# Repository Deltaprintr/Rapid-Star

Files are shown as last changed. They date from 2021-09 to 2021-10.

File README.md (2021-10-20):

Rapid Star Image

# Overview

Rapid Star is a PNP (Pick and Place) system developed and maintained by [Deltaprintr](https://deltaprintr.com), run on the free [OpenPNP Software](https://openpnp.org) and [Mark's Smoothieware Firmware Version](https://makr.zone/smoothieware-new-firmware-for-pnp/500/) used for assembling circuit boards with the [Rapid Feeder](https://www.deltaprintr.com/product/rapid-feeder/) system. It features a conveyor belt that can hold boards up to 165mm (6.5") wide, 50 (8mm) feeders and has a head capable of supporting up to 8 nozzles with a 20 nozzle magazine auto-changer. Documentation on building a Rapid Star can be found [on our website](https://www.deltaprintr.com/docs/rapid-star/). The release is considered stable as the machine has been fully tested manually. If you would like to show your support for the project, consider purchasing [components directly from Deltaprintr](https://www.deltaprintr.com/product-category/smt-assembly/). This not only allows us to continue developing the Rapid Star, but also enables us to provide support directly to you in the process.

If you'd like to find out once Deltaprintr starts offering a complete kit, you can subscribe to our [mailing list](https://mailchi.mp/ee676e0cfc9f/rapidstar)

# Benefits of a star design
- Scalable nozzle count at no additional cost
- Higher CPH
- Simpler mechanical assembly
- More X/Y space due to smaller head, which means more space for feeders/trays.

# Contribute

Currently the Rapid Star is not fully supported in OpenPNP due to a few missing mandatory features. We're actively looking for developers who would be interested in helping us incorporate support into OpenPNP. You can see the [full list of features here](https://docs.google.com/document/d/1N6ggEopUlor0r7kC39QZDpr8pi3T8QCvNgg1l5aPtP0/edit?usp=sharing). If you're interested in helping, let us know on our [Discord Server](https://discord.gg/t2FcjAU7hC)!

If you'd like to keep up with the latest news you can also follow us on [Instagram](https://www.instagram.com/deltaprintr/), [Facebook](https://www.facebook.com/Deltaprintr/) or [Twitter](https://twitter.com/deltaprintr)!

# Support

While you are free to source and build a Rapid Star on your own, we are only able to provide support for customers who purchase components directly from us. This way we can guarantee your parts came from a reputable source and have a warranty. It's worth noting that some custom parts such as the head must be machined to a high tolerance to ensure air does not leak. For this reason, we recommend to get parts directly from us as it will save you time and frustration. However, if you do decide to source parts elsewhere, we do have a community of users who would be happy to help you on our [Discord Server](https://discord.gg/t2FcjAU7hC).

You can view a 3D model of the full assembly in your browser here: https://autode.sk/3zCK5wB

Support questions submitted via Github will be deleted. Only bugs/issues should be submitted via Github.

# Github Structure
- Mechanics (Full machine assembly)
- Electronics (Rapid Board, Conveyor, C Endstop, Nozzle Magazine, Feeder Extension, Feeder Motherboard)
- Firmware (Smoothieware and config)
- Openpnp Settings (OpenPNP machine.xml)
- Jigs (Lens calibration PCB)
- Scripts (Gcode for upward lens cam calibration)

# Programs Used
- Fusion 360
- Eagle CAD

# License

Rapid Star is licensed under [CC BY-NC-SA](https://creativecommons.org/licenses/by-nc-sa/4.0/): This license allows reusers to distribute, remix, adapt, and build upon the material in any medium or format for **non-commercial purposes only**, and only so long as attribution is given to the creator. If you remix, adapt, or build upon the material, you must license the modified material under identical terms. 

CC BY-NC-SA includes the following elements:

* BY  – Credit must be given to the creator
* NC  – Only non-commercial uses of the work are permitted
* SA  – Adaptations must be shared under the same terms

Deltaprintr, Rapid Star and Rapid Feeder are trademarks of Deltaprinter Inc. Other trademarks may be pending.

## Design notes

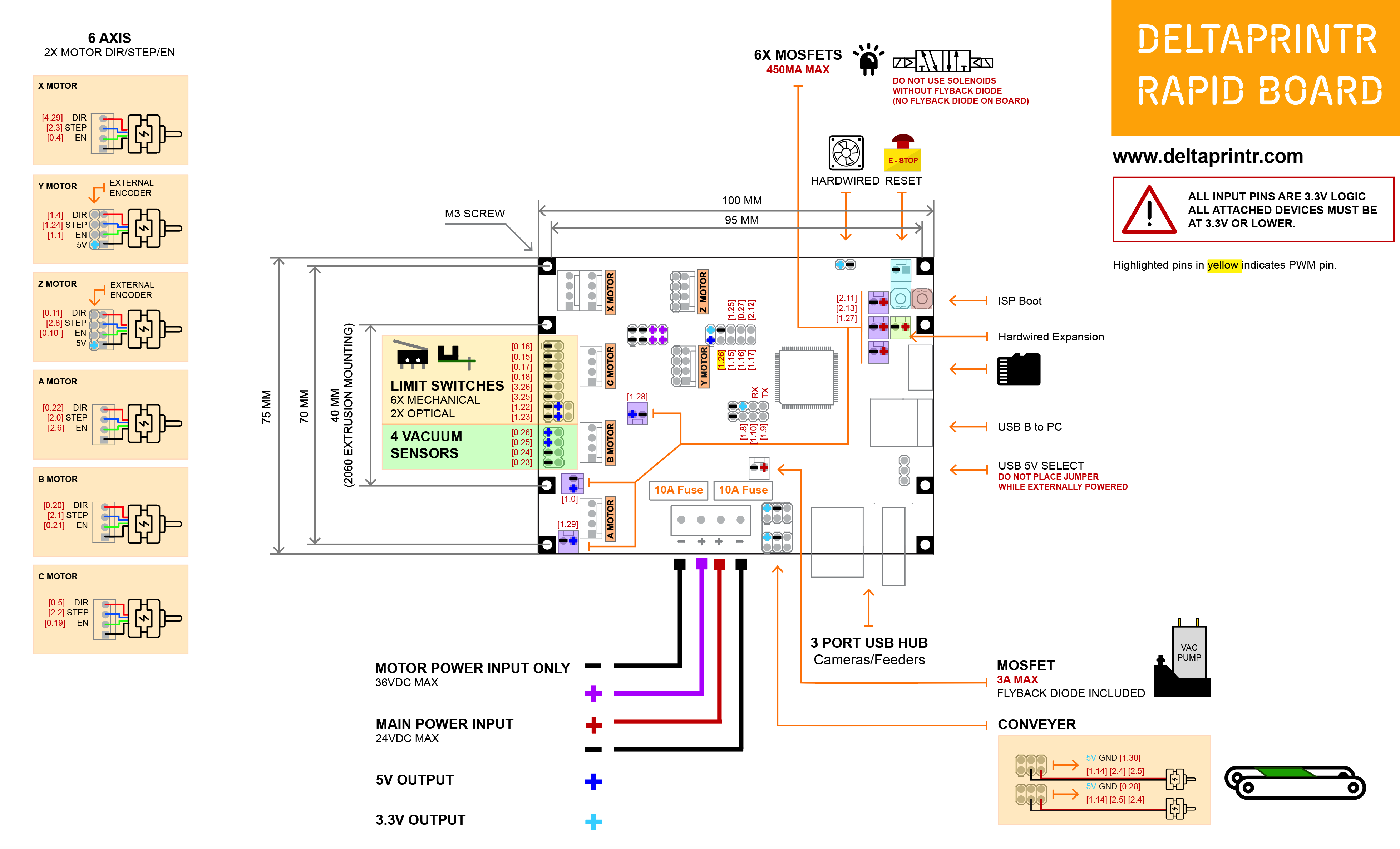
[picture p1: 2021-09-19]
Electronics/Rapid Board/Rapid Board Connections.png

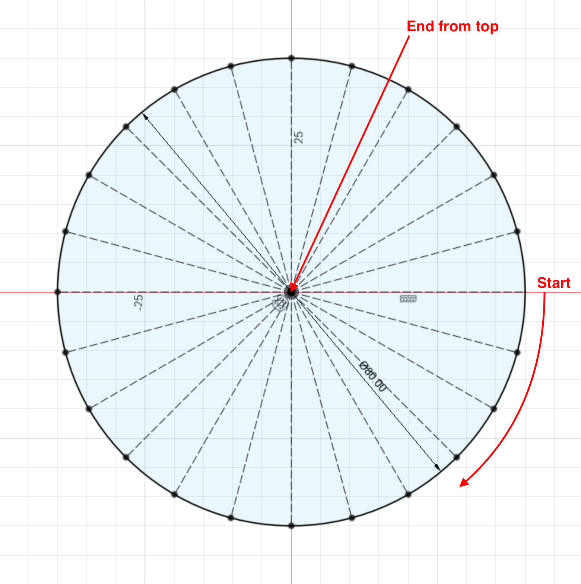
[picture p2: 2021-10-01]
Scripts/Upward Cam Gcode.png

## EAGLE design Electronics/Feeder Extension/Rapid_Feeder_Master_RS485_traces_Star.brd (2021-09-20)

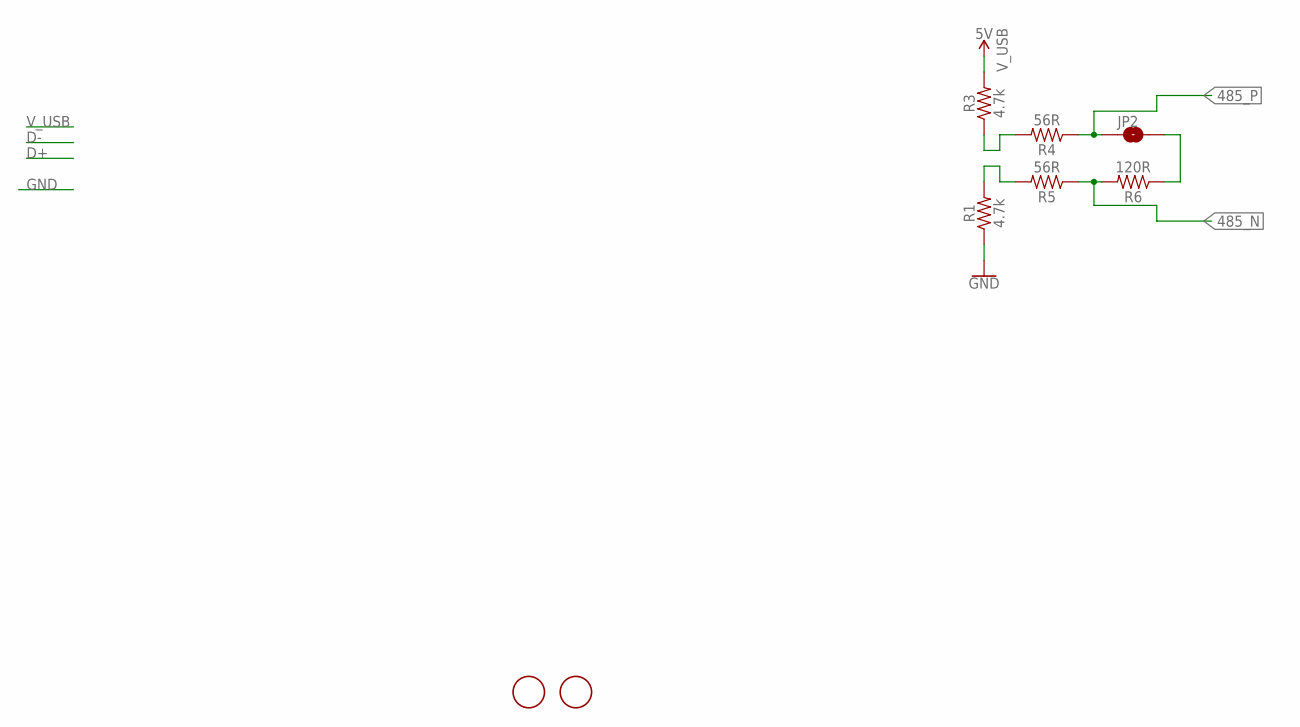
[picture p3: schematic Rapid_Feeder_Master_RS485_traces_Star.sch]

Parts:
JP2: JUMPER-SMT_2_NO_NO-SILK; SMT-JUMPER_2_NO_NO-SILK
R1, R3: 4.7k; R0603
R4, R5: 56R; R0603
R6: 120R; R0603
U$1, U$2: FIDUCIAL; FIDUCIAL_1MM

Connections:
485_N: R5.1, R6.2
485_P: JP2.1, R4.1
GND: R1.1
unnamed: R3.1, R4.2
unnamed: R1.2, R5.2
unnamed: JP2.2, R6.1
V_USB: R3.2

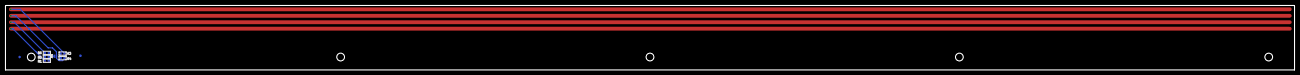
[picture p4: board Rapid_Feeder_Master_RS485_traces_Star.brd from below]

Board: 2 copper layers, 500.0 x 25.0 mm, 8 parts (8 on the bottom side), 5 nets.

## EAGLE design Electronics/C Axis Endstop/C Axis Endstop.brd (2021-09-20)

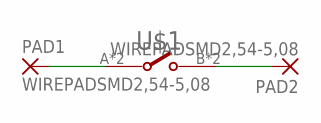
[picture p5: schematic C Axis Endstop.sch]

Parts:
PAD1, PAD2: WIREPADSMD2,54-5,08; SMD2,54-5,08
U$1: SWITCH_LIMIT_HDP001L

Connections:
unnamed: PAD1.1, U$1.A (1), U$1.C (1)
unnamed: PAD2.1, U$1.B (2), U$1.D (2)

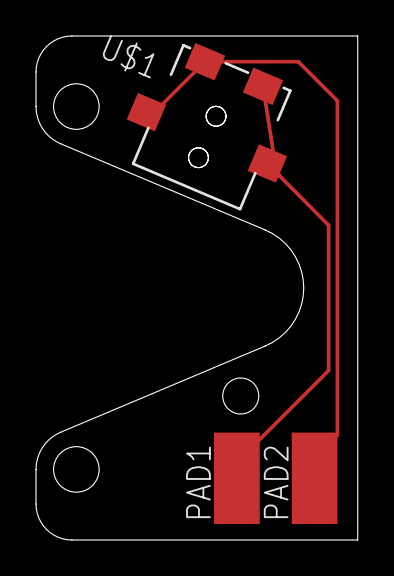
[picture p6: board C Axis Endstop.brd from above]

Board: 2 copper layers, 17.9 x 28.0 mm, 3 parts (0 on the bottom side), 2 nets.

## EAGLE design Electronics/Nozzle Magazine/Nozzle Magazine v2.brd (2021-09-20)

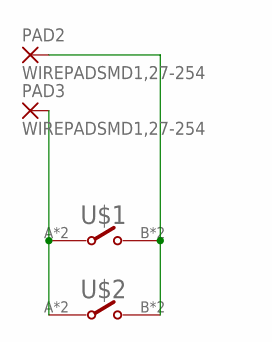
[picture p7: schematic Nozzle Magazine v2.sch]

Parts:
PAD2, PAD3: WIREPADSMD1,27-254; SMD1,27-2,54
U$1, U$2: SWITCH_LIMIT_HDP001L

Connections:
unnamed: PAD3.1, U$1.A (1), U$1.C (1), U$2.A (1), U$2.C (1)
unnamed: PAD2.1, U$1.B (2), U$1.D (2), U$2.B (2), U$2.D (2)

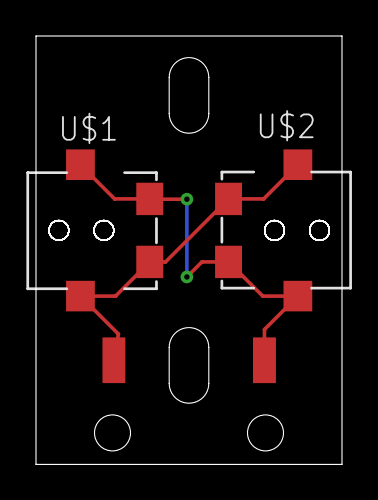
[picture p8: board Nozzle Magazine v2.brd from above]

Board: 2 copper layers, 17.0 x 23.8 mm, 4 parts (0 on the bottom side), 2 nets.

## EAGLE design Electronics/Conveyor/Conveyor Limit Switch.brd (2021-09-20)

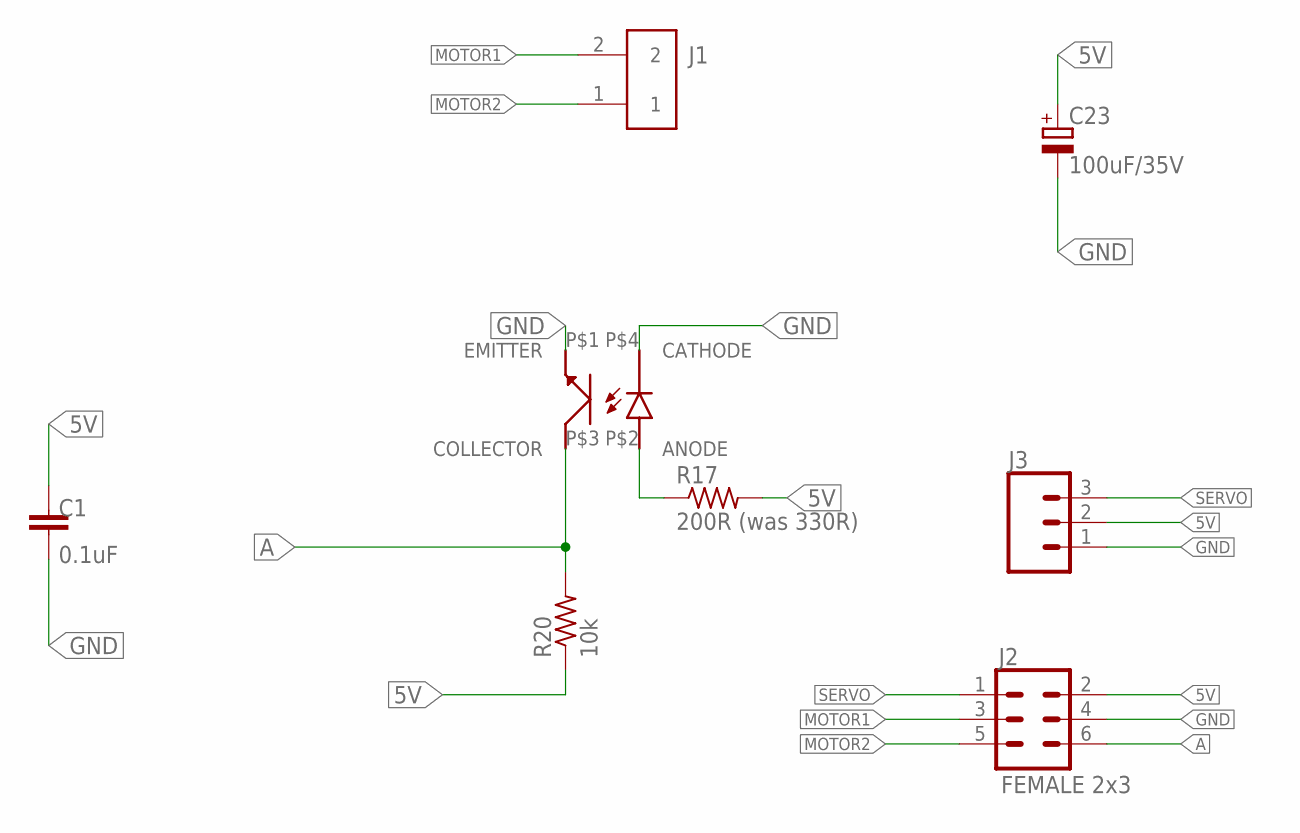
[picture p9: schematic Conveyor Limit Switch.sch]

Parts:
C1: 0.1uF; CAP_0603
C23: 100uF/35V; 153CLV-0605
J1: S2B-PH-SM4-TB(LF)(SN); S2B-PH-SM4-TB
J2: FEMALE 2x3; 2X3
J3: CONN_03; 1X03
R17: 200R (was 330R); RESISTOR_0603
R20: 10k; RESISTOR_0603
U$2: IR_VCNT2020

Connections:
5V: C1.1, C23.+, J2.2, J3.2, R17.2, R20.1
A: J2.6, R20.2, U$2.P$3 (COLLECTOR)
GND: C1.2, C23.-, J2.4, J3.1, U$2.P$1 (EMITTER), U$2.P$4 (CATHODE)
LED2: R17.1, U$2.P$2 (ANODE)
MOTOR1: J1.2, J2.3
MOTOR2: J1.1, J2.5
SERVO: J2.1, J3.3

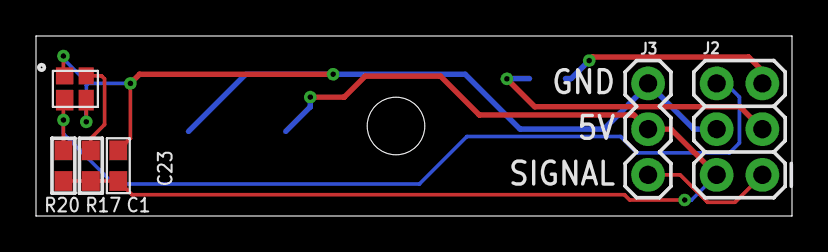
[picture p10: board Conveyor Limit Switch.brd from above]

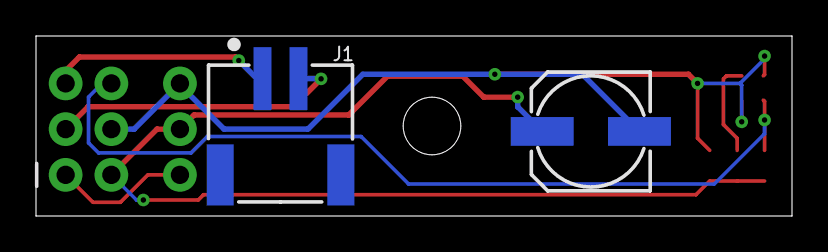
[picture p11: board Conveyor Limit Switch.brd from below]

Board: 2 copper layers, 42.0 x 10.0 mm, 8 parts (2 on the bottom side), 7 nets.

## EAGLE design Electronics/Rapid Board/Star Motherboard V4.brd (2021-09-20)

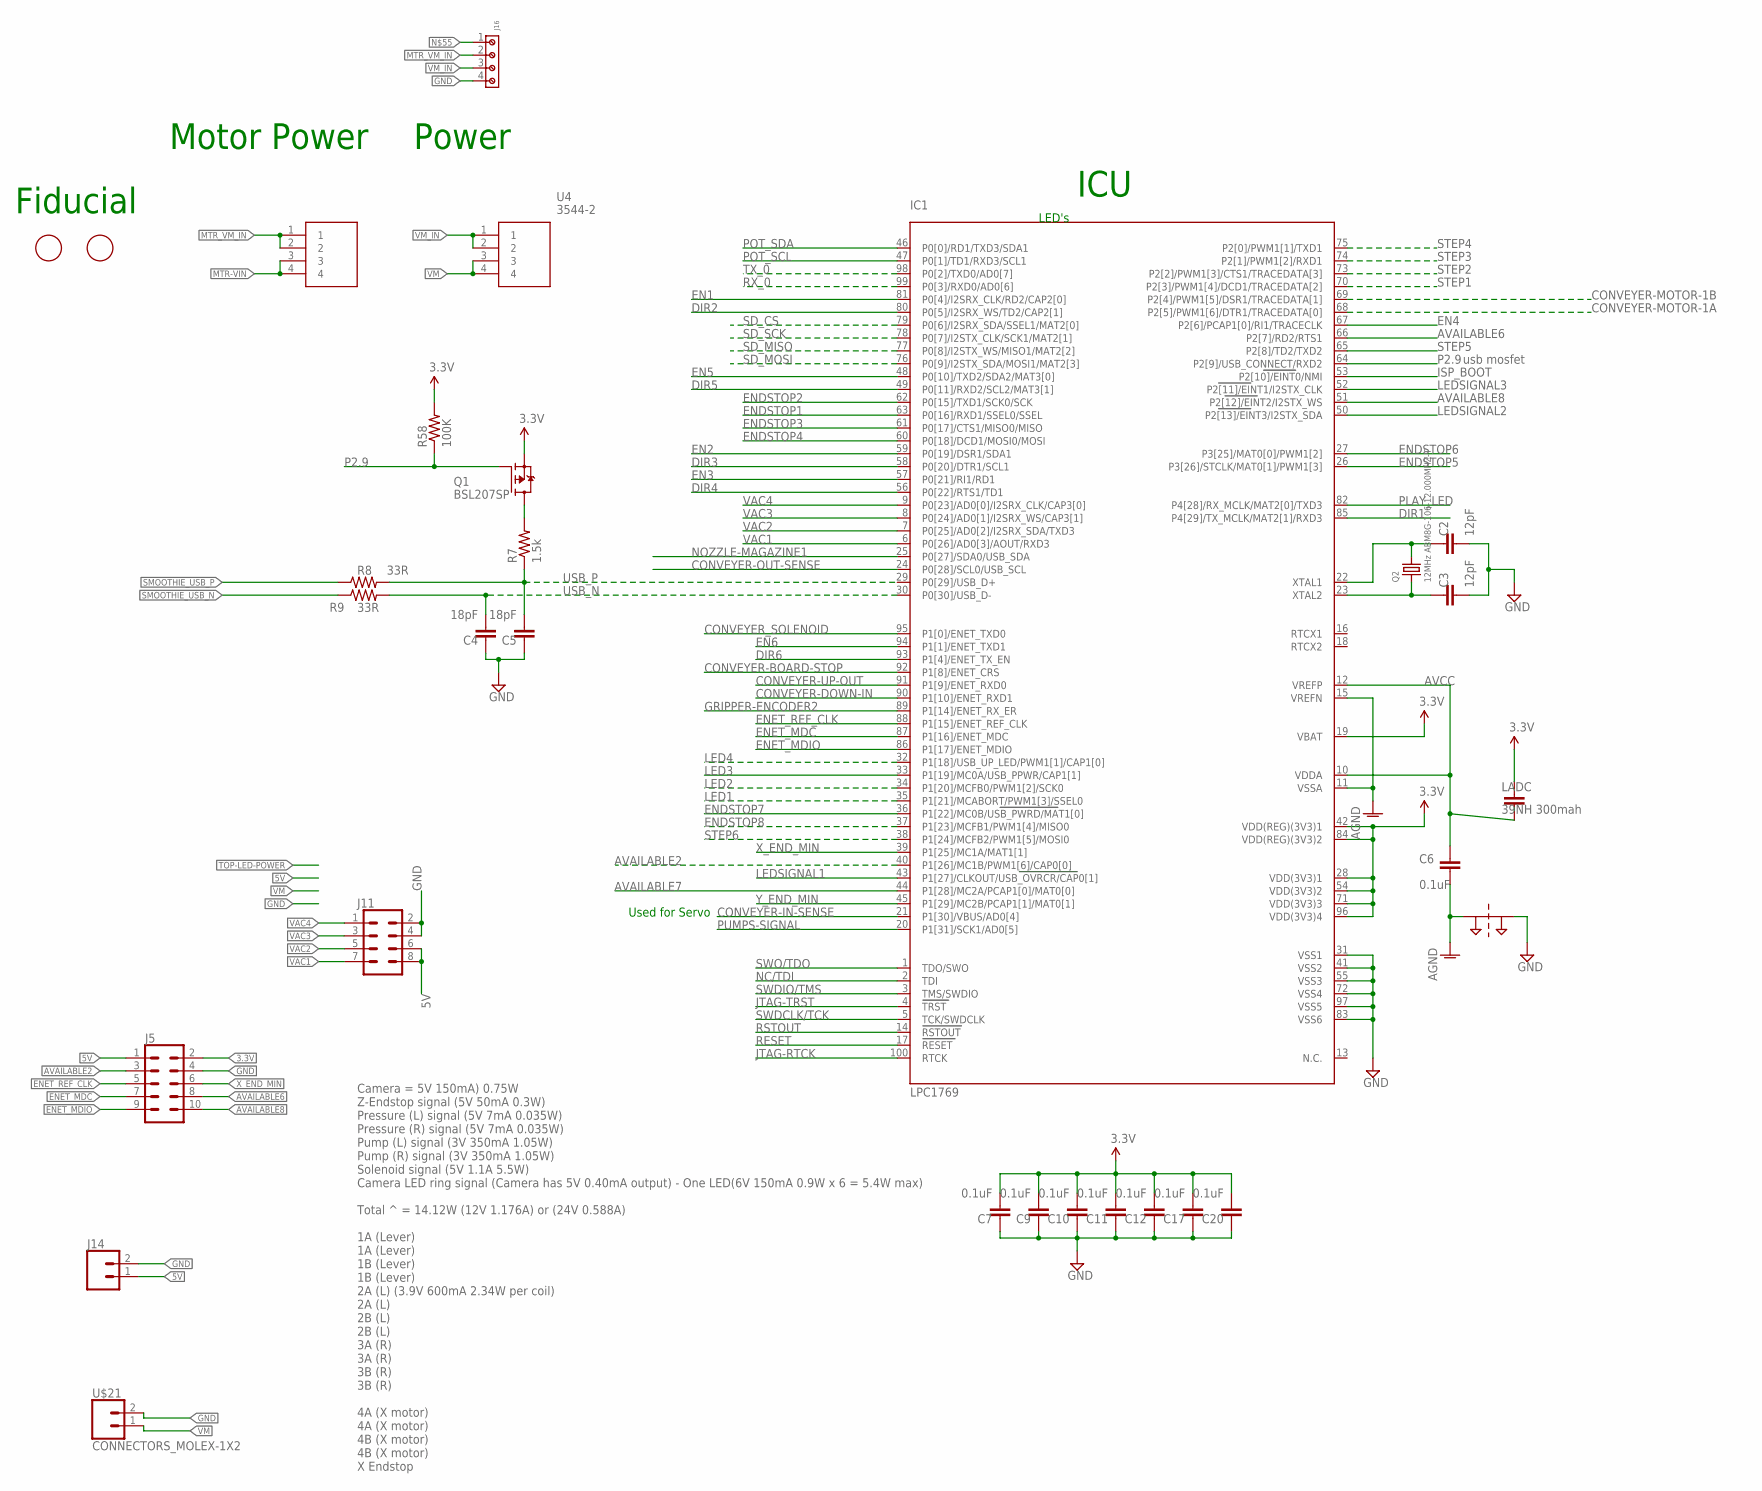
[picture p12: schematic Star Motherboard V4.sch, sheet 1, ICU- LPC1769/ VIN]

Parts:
C2, C3: 12pF; CAP_0603
C4, C5: 18pF; CAP_0603
C6, C7, C9, C10, C11, C12, C17, C20: 0.1uF; CAP_0603
IC1: LPC1769
J5: CONN_05X2PTH; 2X5
J11: CONN_04X2; 2X4
J14: CONN_02; 1X02
J16: 691137710004
LADC: 39NH 300mah; CAP_0603
Q1: BSL207SP; SC74_INFINEON
Q2: 12MHz ABM8G-106-12.000MHZ-T; CRYSTAL_3.2X2.5
R7: 1.5k; RESISTOR_0603
R8, R9: 33R; RESISTOR_0603
R58: 100K; RESISTOR_0603
SUPPLY10: 2PT_GND_TIE
U1, U4: 3544-2
U$9, U$10: FIDUCIAL; FIDUCIAL_1MM
U$21: CONNECTORS_MOLEX-1X2

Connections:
3.3V: C7.2, C9.2, C10.2, C11.2, C12.2, C17.2, C20.2, IC1.19 (VBAT), IC1.28 (VDD(3V3)1), IC1.42 (VDD(REG)(3V3)1), IC1.54 (VDD(3V3)2), IC1.71 (VDD(3V3)3), IC1.84 (VDD(REG)(3V3)2), IC1.96 (VDD(3V3)4), J5.2, LADC.1, Q1.4 (S), R58.2; also elsewhere on the board
5V: J5.1, J11.6, J11.8, J14.1; also elsewhere on the board
AGND: C6.2, IC1.11 (VSSA), IC1.15 (VREFN), SUPPLY10.P$1; also elsewhere on the board
AVAILABLE2: IC1.40 (P1[26]/MC1B/PWM1[6]/CAP0[0]), J5.3
AVAILABLE6: IC1.66 (P2[7]/RD2/RTS1), J5.8
AVAILABLE7: IC1.44 (P1[28]/MC2A/PCAP1[0]/MAT0[0]); also elsewhere on the board
AVAILABLE8: IC1.51 (P2[12]/EINT2/I2STX_WS), J5.10
AVCC: C6.1, IC1.10 (VDDA), IC1.12 (VREFP), LADC.2; also elsewhere on the board
CONVEYER-BOARD-STOP: IC1.92 (P1[8]/ENET_CRS); also elsewhere on the board
CONVEYER-DOWN-IN: IC1.90 (P1[10]/ENET_RXD1); also elsewhere on the board
CONVEYER-IN-SENSE: IC1.21 (P1[30]/VBUS/AD0[4]); also elsewhere on the board
CONVEYER-MOTOR-1A: IC1.68 (P2[5]/PWM1[6]/DTR1/TRACEDATA[0]); also elsewhere on the board
CONVEYER-MOTOR-1B: IC1.69 (P2[4]/PWM1[5]/DSR1/TRACEDATA[1]); also elsewhere on the board
CONVEYER-OUT-SENSE: IC1.24 (P0[28]/SCL0/USB_SCL); also elsewhere on the board
CONVEYER-UP-OUT: IC1.91 (P1[9]/ENET_RXD0); also elsewhere on the board
CONVEYER_SOLENOID: IC1.95 (P1[0]/ENET_TXD0); also elsewhere on the board
DIR1: IC1.85 (P4[29]/TX_MCLK/MAT2[1]/RXD3); also elsewhere on the board
DIR2: IC1.80 (P0[5]/I2SRX_WS/TD2/CAP2[1]); also elsewhere on the board
DIR3: IC1.58 (P0[20]/DTR1/SCL1); also elsewhere on the board
DIR4: IC1.56 (P0[22]/RTS1/TD1); also elsewhere on the board
DIR5: IC1.49 (P0[11]/RXD2/SCL2/MAT3[1]); also elsewhere on the board
DIR6: IC1.93 (P1[4]/ENET_TX_EN); also elsewhere on the board
EN1: IC1.81 (P0[4]/I2SRX_CLK/RD2/CAP2[0]); also elsewhere on the board
EN2: IC1.59 (P0[19]/DSR1/SDA1); also elsewhere on the board
EN3: IC1.57 (P0[21]/RI1/RD1); also elsewhere on the board
EN4: IC1.67 (P2[6]/PCAP1[0]/RI1/TRACECLK); also elsewhere on the board
EN5: IC1.48 (P0[10]/TXD2/SDA2/MAT3[0]); also elsewhere on the board
EN6: IC1.94 (P1[1]/ENET_TXD1); also elsewhere on the board
ENDSTOP1: IC1.63 (P0[16]/RXD1/SSEL0/SSEL); also elsewhere on the board
ENDSTOP2: IC1.62 (P0[15]/TXD1/SCK0/SCK); also elsewhere on the board
ENDSTOP3: IC1.61 (P0[17]/CTS1/MISO0/MISO); also elsewhere on the board
ENDSTOP4: IC1.60 (P0[18]/DCD1/MOSI0/MOSI); also elsewhere on the board
ENDSTOP5: IC1.26 (P3[26]/STCLK/MAT0[1]/PWM1[3]); also elsewhere on the board
ENDSTOP6: IC1.27 (P3[25]/MAT0[0]/PWM1[2]); also elsewhere on the board
ENDSTOP7: IC1.36 (P1[22]/MC0B/USB_PWRD/MAT1[0]); also elsewhere on the board
ENDSTOP8: IC1.37 (P1[23]/MCFB1/PWM1[4]/MISO0); also elsewhere on the board
ENET_MDC: IC1.87 (P1[16]/ENET_MDC), J5.7
ENET_MDIO: IC1.86 (P1[17]/ENET_MDIO), J5.9
ENET_REF_CLK: IC1.88 (P1[15]/ENET_REF_CLK), J5.5
GND: C2.2, C3.2, C4.1, C5.1, C7.1, C9.1, C10.1, C11.1, C12.1, C17.1, C20.1, IC1.31 (VSS1), IC1.41 (VSS2), IC1.55 (VSS3), IC1.72 (VSS4), IC1.83 (VSS6), IC1.97 (VSS5), J5.4, J11.2, J11.4, J14.2, J16.4, SUPPLY10.P$2, U$21.2; also elsewhere on the board
GRIPPER-ENCODER2: IC1.89 (P1[14]/ENET_RX_ER); also elsewhere on the board
ISP_BOOT: IC1.53 (P2[10]/EINT0/NMI); also elsewhere on the board
JTAG-RTCK: IC1.100 (RTCK)
JTAG-TRST: IC1.4 (TRST)
LED1: IC1.35 (P1[21]/MCABORT/PWM1[3]/SSEL0); also elsewhere on the board
LED2: IC1.34 (P1[20]/MCFB0/PWM1[2]/SCK0); also elsewhere on the board
LED3: IC1.33 (P1[19]/MC0A/USB_PPWR/CAP1[1]); also elsewhere on the board
LED4: IC1.32 (P1[18]/USB_UP_LED/PWM1[1]/CAP1[0]); also elsewhere on the board
LEDSIGNAL1: IC1.43 (P1[27]/CLKOUT/USB_OVRCR/CAP0[1]); also elsewhere on the board
LEDSIGNAL2: IC1.50 (P2[13]/EINT3/I2STX_SDA); also elsewhere on the board
LEDSIGNAL3: IC1.52 (P2[11]/EINT1/I2STX_CLK); also elsewhere on the board
MTR-VIN: U1.3, U1.4; also elsewhere on the board
MTR_VM_IN: J16.2, U1.1, U1.2
unnamed: C2.1, IC1.22 (XTAL1), Q2.2
unnamed: C3.1, IC1.23 (XTAL2), Q2.1
unnamed: Q1.1 (D), Q1.2 (D), Q1.5 (D), Q1.6 (D), R7.2
NC/TDI: IC1.2 (TDI)
NOZZLE-MAGAZINE1: IC1.25 (P0[27]/SDA0/USB_SDA); also elsewhere on the board
P2.9: IC1.64 (P2[9]/USB_CONNECT/RXD2), Q1.3 (G), R58.1
PLAY_LED: IC1.82 (P4[28]/RX_MCLK/MAT2[0]/TXD3); also elsewhere on the board
POT_SCL: IC1.47 (P0[1]/TD1/RXD3/SCL1); also elsewhere on the board
POT_SDA: IC1.46 (P0[0]/RD1/TXD3/SDA1); also elsewhere on the board
PUMPS-SIGNAL: IC1.20 (P1[31]/SCK1/AD0[5]); also elsewhere on the board
RESET: IC1.17 (RESET); also elsewhere on the board
RSTOUT: IC1.14 (RSTOUT)
RX_0: IC1.99 (P0[3]/RXD0/AD0[6]); also elsewhere on the board
SD_CS: IC1.79 (P0[6]/I2SRX_SDA/SSEL1/MAT2[0]); also elsewhere on the board
SD_MISO: IC1.77 (P0[8]/I2STX_WS/MISO1/MAT2[2]); also elsewhere on the board
SD_MOSI: IC1.76 (P0[9]/I2STX_SDA/MOSI1/MAT2[3]); also elsewhere on the board
SD_SCK: IC1.78 (P0[7]/I2STX_CLK/SCK1/MAT2[1]); also elsewhere on the board
SMOOTHIE_USB_N: R9.1; also elsewhere on the board
SMOOTHIE_USB_P: R8.1; also elsewhere on the board
STEP1: IC1.70 (P2[3]/PWM1[4]/DCD1/TRACEDATA[2]); also elsewhere on the board
STEP2: IC1.73 (P2[2]/PWM1[3]/CTS1/TRACEDATA[3]); also elsewhere on the board
STEP3: IC1.74 (P2[1]/PWM1[2]/RXD1); also elsewhere on the board
STEP4: IC1.75 (P2[0]/PWM1[1]/TXD1); also elsewhere on the board
STEP5: IC1.65 (P2[8]/TD2/TXD2); also elsewhere on the board
STEP6: IC1.38 (P1[24]/MCFB2/PWM1[5]/MOSI0); also elsewhere on the board
SWDCLK/TCK: IC1.5 (TCK/SWDCLK)
SWDIO/TMS: IC1.3 (TMS/SWDIO)
SWO/TDO: IC1.1 (TDO/SWO)
TX_0: IC1.98 (P0[2]/TXD0/AD0[7]); also elsewhere on the board
USB_N: C4.2, IC1.30 (P0[30]/USB_D-), R9.2
USB_P: C5.2, IC1.29 (P0[29]/USB_D+), R7.1, R8.2
VAC1: IC1.6 (P0[26]/AD0[3]/AOUT/RXD3), J11.7; also elsewhere on the board
VAC2: IC1.7 (P0[25]/AD0[2]/I2SRX_SDA/TXD3), J11.5; also elsewhere on the board
VAC3: IC1.8 (P0[24]/AD0[1]/I2SRX_WS/CAP3[1]), J11.3; also elsewhere on the board
VAC4: IC1.9 (P0[23]/AD0[0]/I2SRX_CLK/CAP3[0]), J11.1; also elsewhere on the board
VM: U4.3, U4.4, U$21.1; also elsewhere on the board
VM_IN: J16.3, U4.1, U4.2
X_END_MIN: IC1.39 (P1[25]/MC1A/MAT1[1]), J5.6
Y_END_MIN: IC1.45 (P1[29]/MC2B/PCAP1[1]/MAT0[1]); also elsewhere on the board

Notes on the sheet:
usb mosfet
LED's
ICU
Fiducial
Power
Camera = 5V 150mA) 0.75W Z-Endstop signal (5V 50mA 0.3W) Pressure (L) signal (5V 7mA 0.035W) Pressure (R) signal (5V 7mA 0.035W) Pump (L) signal (3V 350mA 1.05W) Pump (R) signal (3V 350mA 1.05W) Solenoid signal (5V 1.1A 5.5W) Camera LED ring signal (Camera has 5V 0.40mA output) - One LED(6V 150mA 0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
Used for Servo
Motor Power

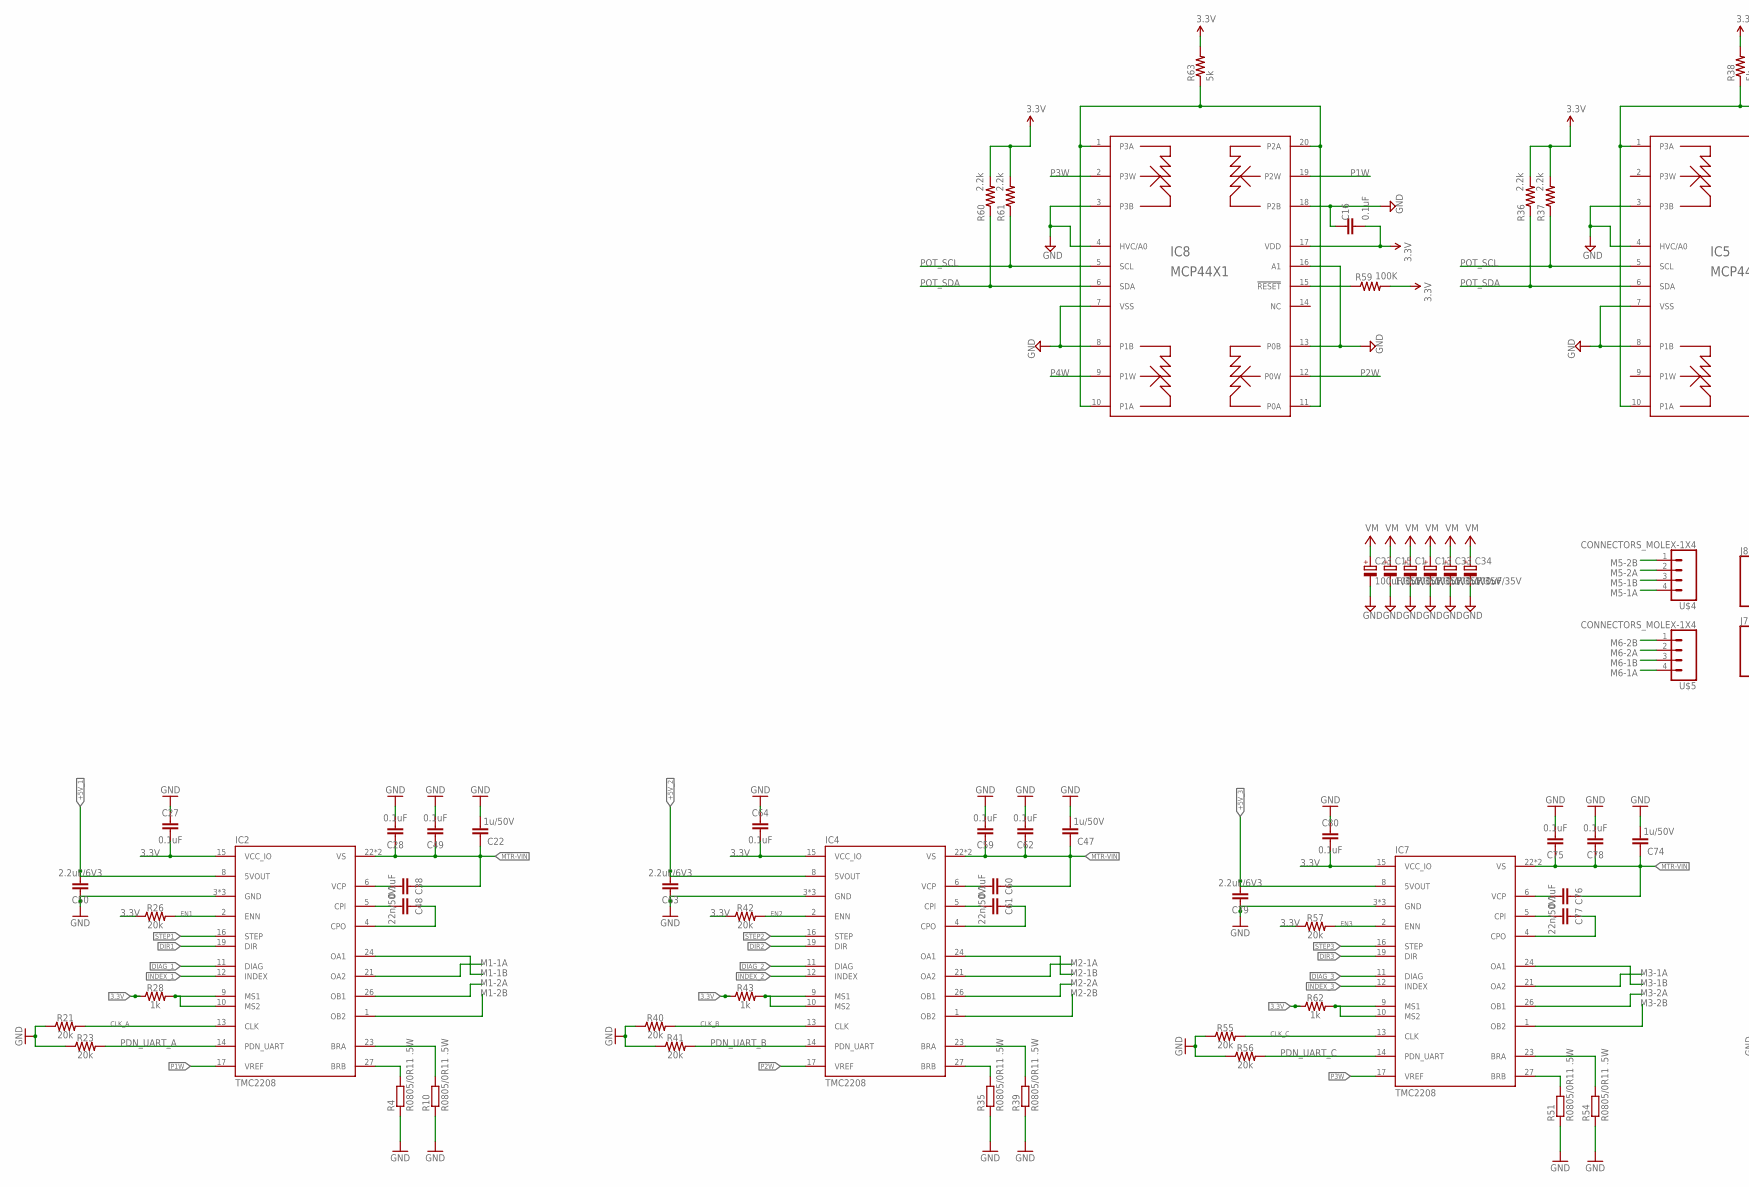
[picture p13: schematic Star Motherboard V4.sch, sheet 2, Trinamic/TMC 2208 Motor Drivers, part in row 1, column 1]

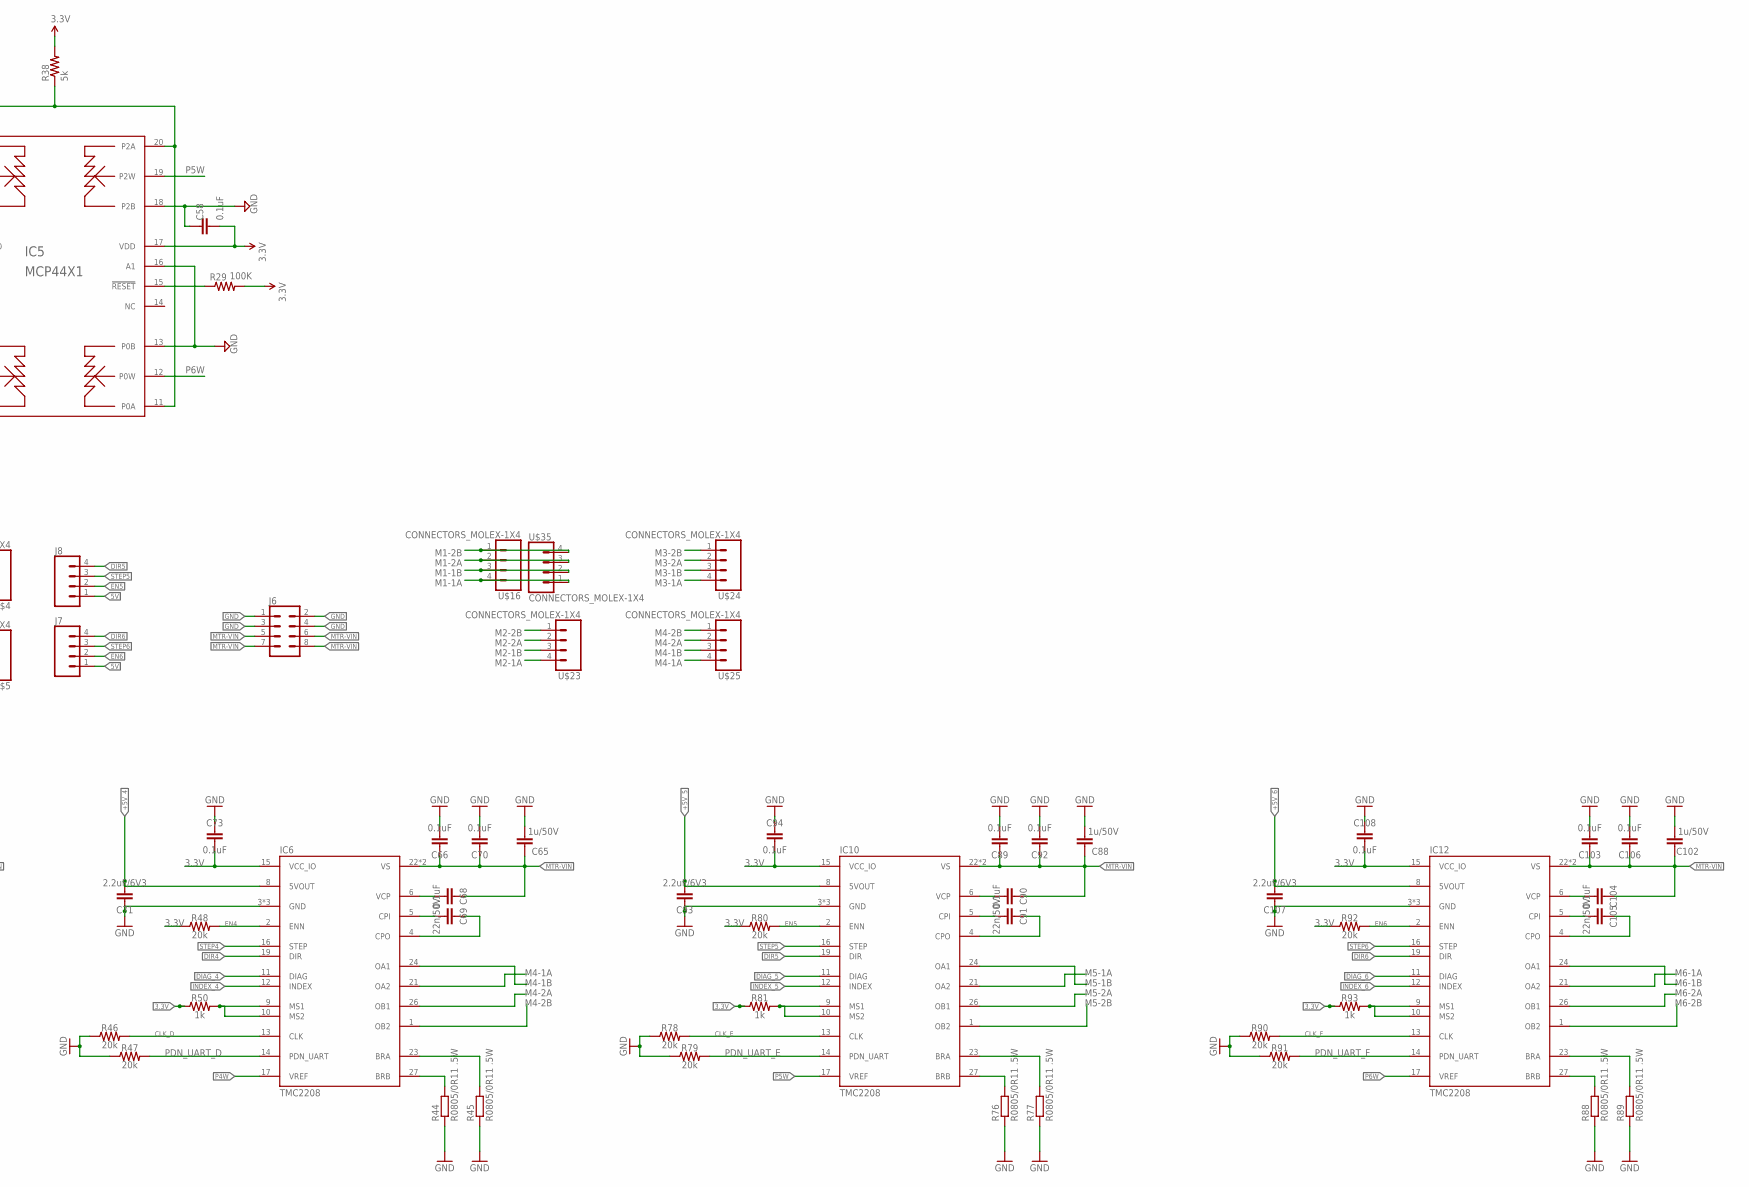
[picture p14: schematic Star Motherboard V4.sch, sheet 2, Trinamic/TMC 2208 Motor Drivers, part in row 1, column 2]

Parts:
C1, C13, C15, C23, C33, C34: 100uF/35V; 153CLV-0605
C16, C27, C28, C38, C49, C58, C59, C60, C62, C64, C66, C68, C70, C73, C75, C76, C78, C80, C89, C90, C92, C94, C103, C104, C106, C108: 0.1uF; CAP_0603
C22, C47, C65, C74, C88, C102: 1u/50V; C0805
C48, C61, C69, C77, C91, C105: 22n/50V; CAP_0603
C50, C63, C71, C79, C93, C107: 2.2uF/6V3; CAP_0603
IC2, IC4, IC6, IC7, IC10, IC12: TMC2208; QFN28-PAD
IC5, IC8: MCP44X1; TSSOP20
J6: CONN_04X2; 2X4
J7, J8: CONN_04; 1X04
R4, R10, R35, R39, R44, R45, R51, R54, R76, R77, R88, R89: R0805/0R11 .5W; R0805
R21, R23, R26, R40, R41, R42, R46, R47, R48, R55, R56, R57, R78, R79, R80, R90, R91, R92: 20k; RESISTOR_0603
R28, R43, R50, R62, R81, R93: 1k; RESISTOR_0603
R29, R59: 100K; RESISTOR_0603
R36, R37, R60, R61: 2.2k; RESISTOR_0603
R38, R63: 5k; RESISTOR_0603
U$4, U$5, U$16, U$23, U$24, U$25, U$35: CONNECTORS_MOLEX-1X4

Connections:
3.3V: C16.2, C27.2, C58.2, C64.2, C73.2, C80.2, C94.2, C108.2, IC2.15 (VCC_IO), IC4.15 (VCC_IO), IC5.17 (VDD), IC6.15 (VCC_IO), IC7.15 (VCC_IO), IC8.17 (VDD), IC10.15 (VCC_IO), IC12.15 (VCC_IO), R26.1, R28.1, R29.2, R36.2, R37.2, R38.2, R42.1, R43.1, R48.1, R50.1, R57.1, R59.2, R60.2, R61.2, R62.1, R63.2, R80.1, R81.1, R92.1, R93.1; also elsewhere on the board
5V: J7.1, J8.1; also elsewhere on the board
+5V_1: C50.2, IC2.8 (5VOUT)
+5V_2: C63.2, IC4.8 (5VOUT)
+5V_3: C79.2, IC7.8 (5VOUT)
+5V_4: C71.2, IC6.8 (5VOUT)
+5V_5: C93.2, IC10.8 (5VOUT)
+5V_6: C107.2, IC12.8 (5VOUT)
BRA2: IC2.23 (BRA), R10.2
BRA3: IC4.23 (BRA), R39.2
BRA4: IC6.23 (BRA), R45.2
BRA5: IC7.23 (BRA), R54.2
BRA7: IC10.23 (BRA), R77.2
BRA9: IC12.23 (BRA), R89.2
BRB2: IC2.27 (BRB), R4.2
BRB3: IC4.27 (BRB), R35.2
BRB4: IC6.27 (BRB), R44.2
BRB5: IC7.27 (BRB), R51.2
BRB7: IC10.27 (BRB), R76.2
BRB9: IC12.27 (BRB), R88.2
CLK_A: IC2.13 (CLK), R21.2
CLK_B: IC4.13 (CLK), R40.2
CLK_C: IC7.13 (CLK), R55.2
CLK_D: IC6.13 (CLK), R46.2
CLK_E: IC10.13 (CLK), R78.2
CLK_F: IC12.13 (CLK), R90.2
CPI2: C48.2, IC2.5 (CPI)
CPI3: C61.2, IC4.5 (CPI)
CPI4: C69.2, IC6.5 (CPI)
CPI6: C77.2, IC7.5 (CPI)
CPI8: C91.2, IC10.5 (CPI)
CPI10: C105.2, IC12.5 (CPI)
CPO2: C48.1, IC2.4 (CPO)
CPO3: C61.1, IC4.4 (CPO)
CPO4: C69.1, IC6.4 (CPO)
CPO6: C77.1, IC7.4 (CPO)
CPO8: C91.1, IC10.4 (CPO)
CPO10: C105.1, IC12.4 (CPO)
DIAG_1: IC2.11 (DIAG)
DIAG_2: IC4.11 (DIAG)
DIAG_3: IC7.11 (DIAG)
DIAG_4: IC6.11 (DIAG)
DIAG_5: IC10.11 (DIAG)
DIAG_6: IC12.11 (DIAG)
DIR1: IC2.19 (DIR); also elsewhere on the board
DIR2: IC4.19 (DIR); also elsewhere on the board
DIR3: IC7.19 (DIR); also elsewhere on the board
DIR4: IC6.19 (DIR); also elsewhere on the board
DIR5: IC10.19 (DIR), J8.4; also elsewhere on the board
DIR6: IC12.19 (DIR), J7.4; also elsewhere on the board
EN1: IC2.2 (ENN), R26.2; also elsewhere on the board
EN2: IC4.2 (ENN), R42.2; also elsewhere on the board
EN3: IC7.2 (ENN), R57.2; also elsewhere on the board
EN4: IC6.2 (ENN), R48.2; also elsewhere on the board
EN5: IC10.2 (ENN), J8.2, R80.2; also elsewhere on the board
EN6: IC12.2 (ENN), J7.2, R92.2; also elsewhere on the board
GND: C1.-, C13.-, C15.-, C16.1, C22.2, C23.-, C27.1, C28.2, C33.-, C34.-, C47.2, C49.2, C50.1, C58.1, C59.2, C62.2, C63.1, C64.1, C65.2, C66.2, C70.2, C71.1, C73.1, C74.2, C75.2, C78.2, C79.1, C80.1, C88.2, C89.2, C92.2, C93.1, C94.1, C102.2, C103.2, C106.2, C107.1, C108.1, IC2.3 (GND), IC2.18 (GND), IC2.TP (GND), IC4.3 (GND), IC4.18 (GND), IC4.TP (GND), IC5.3 (P3B), IC5.4 (HVC/A0), IC5.7 (VSS), IC5.8 (P1B), IC5.13 (P0B), IC5.16 (A1), IC5.18 (P2B), IC6.3 (GND), IC6.18 (GND), IC6.TP (GND), IC7.3 (GND), IC7.18 (GND), IC7.TP (GND), IC8.3 (P3B), IC8.4 (HVC/A0), IC8.7 (VSS), IC8.8 (P1B), IC8.13 (P0B), IC8.16 (A1), IC8.18 (P2B), IC10.3 (GND), IC10.18 (GND), IC10.TP (GND), IC12.3 (GND), IC12.18 (GND), IC12.TP (GND), J6.1, J6.2, J6.3, J6.4, R4.1, R10.1, R21.1, R23.1, R35.1, R39.1, R40.1, R41.1, R44.1, R45.1, R46.1, R47.1, R51.1, R54.1, R55.1, R56.1, R76.1, R77.1, R78.1, R79.1, R88.1, R89.1, R90.1, R91.1; also elsewhere on the board
INDEX_1: IC2.12 (INDEX)
INDEX_2: IC4.12 (INDEX)
INDEX_3: IC7.12 (INDEX)
INDEX_4: IC6.12 (INDEX)
INDEX_5: IC10.12 (INDEX)
INDEX_6: IC12.12 (INDEX)
M1-1A: IC2.21 (OA2), U$16.4, U$35.1
M1-1B: IC2.24 (OA1), U$16.3, U$35.2
M1-2A: IC2.26 (OB1), U$16.2, U$35.3
M1-2B: IC2.1 (OB2), U$16.1, U$35.4
M2-1A: IC4.21 (OA2), U$23.4
M2-1B: IC4.24 (OA1), U$23.3
M2-2A: IC4.26 (OB1), U$23.2
M2-2B: IC4.1 (OB2), U$23.1
M3-1A: IC7.21 (OA2), U$24.4
M3-1B: IC7.24 (OA1), U$24.3
M3-2A: IC7.26 (OB1), U$24.2
M3-2B: IC7.1 (OB2), U$24.1
M4-1A: IC6.21 (OA2), U$25.4
M4-1B: IC6.24 (OA1), U$25.3
M4-2A: IC6.26 (OB1), U$25.2
M4-2B: IC6.1 (OB2), U$25.1
M5-1A: IC10.21 (OA2), U$4.4
M5-1B: IC10.24 (OA1), U$4.3
M5-2A: IC10.26 (OB1), U$4.2
M5-2B: IC10.1 (OB2), U$4.1
M6-1A: IC12.21 (OA2), U$5.4
M6-1B: IC12.24 (OA1), U$5.3
M6-2A: IC12.26 (OB1), U$5.2
M6-2B: IC12.1 (OB2), U$5.1
MSX2: IC2.9 (MS1), IC2.10 (MS2), R28.2
MSX3: IC4.9 (MS1), IC4.10 (MS2), R43.2
MSX4: IC6.9 (MS1), IC6.10 (MS2), R50.2
MSX5: IC7.9 (MS1), IC7.10 (MS2), R62.2
MSX7: IC10.9 (MS1), IC10.10 (MS2), R81.2
MSX9: IC12.9 (MS1), IC12.10 (MS2), R93.2
MTR-VIN: C1.+, C13.+, C15.+, C22.1, C23.+, C28.1, C33.+, C34.+, C38.1, C47.1, C49.1, C59.1, C60.1, C62.1, C65.1, C66.1, C68.1, C70.1, C74.1, C75.1, C76.1, C78.1, C88.1, C89.1, C90.1, C92.1, C102.1, C103.1, C104.1, C106.1, IC2.22 (VS), IC2.28 (VS), IC4.22 (VS), IC4.28 (VS), IC6.22 (VS), IC6.28 (VS), IC7.22 (VS), IC7.28 (VS), IC10.22 (VS), IC10.28 (VS), IC12.22 (VS), IC12.28 (VS), J6.5, J6.6, J6.7, J6.8; also elsewhere on the board
unnamed: IC8.15 (!RESET), R59.1
unnamed: IC8.1 (P3A), IC8.10 (P1A), IC8.11 (P0A), IC8.20 (P2A), R63.1
unnamed: IC5.15 (!RESET), R29.1
unnamed: IC5.1 (P3A), IC5.10 (P1A), IC5.11 (P0A), IC5.20 (P2A), R38.1
P1W: IC2.17 (VREF), IC8.19 (P2W)
P2W: IC4.17 (VREF), IC8.12 (P0W)
P3W: IC7.17 (VREF), IC8.2 (P3W)
P4W: IC6.17 (VREF), IC8.9 (P1W)
P5W: IC5.19 (P2W), IC10.17 (VREF)
P6W: IC5.12 (P0W), IC12.17 (VREF)
PDN_UART_A: IC2.14 (PDN_UART), R23.2
PDN_UART_B: IC4.14 (PDN_UART), R41.2
PDN_UART_C: IC7.14 (PDN_UART), R56.2
PDN_UART_D: IC6.14 (PDN_UART), R47.2
PDN_UART_E: IC10.14 (PDN_UART), R79.2
PDN_UART_F: IC12.14 (PDN_UART), R91.2
POT_SCL: IC5.5 (SCL), IC8.5 (SCL), R37.1, R61.1; also elsewhere on the board
POT_SDA: IC5.6 (SDA), IC8.6 (SDA), R36.1, R60.1; also elsewhere on the board
STEP1: IC2.16 (STEP); also elsewhere on the board
STEP2: IC4.16 (STEP); also elsewhere on the board
STEP3: IC7.16 (STEP); also elsewhere on the board
STEP4: IC6.16 (STEP); also elsewhere on the board
STEP5: IC10.16 (STEP), J8.3; also elsewhere on the board
STEP6: IC12.16 (STEP), J7.3; also elsewhere on the board
VCP2: C38.2, IC2.6 (VCP)
VCP3: C60.2, IC4.6 (VCP)
VCP4: C68.2, IC6.6 (VCP)
VCP6: C76.2, IC7.6 (VCP)
VCP8: C90.2, IC10.6 (VCP)
VCP10: C104.2, IC12.6 (VCP)


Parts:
22UH: 22uH; CD75
C18: 10uF; CAP_0603
C24, C25: 10uF; C0805
C35, C36, C39: 0.1uF; CAP_0603
C37: 18pF; CAP_0603
C40: 100uF/35V; 153CLV-0605
D4: B260A-13-F; DO-214AC
R11, R15: 49.9k/1%; RESISTOR_0603
R25: 9.53k/1%; RESISTOR_0603
U2: LM1117; SOT223
U$2: AOZ1282CI; SOT23-6

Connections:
3.3V: C18.1, U2.2 (OUT), U2.4 (OUT); also elsewhere on the board
5V: 22UH.1, C24.1, C25.1, C39.1, R15.1, U2.3 (IN); also elsewhere on the board
GND: C18.2, C24.2, C25.2, C35.2, C37.2, C39.2, C40.-, D4.2 (A), R25.2, U2.1 (ADJ), U$2.2 (GND); also elsewhere on the board
unnamed: R11.1, U$2.4 (EN)
unnamed: C36.2, U$2.1 (BST)
unnamed: 22UH.2, C36.1, D4.1 (C), U$2.6 (LX)
unnamed: C37.1, R15.2, R25.1, U$2.3 (FB)
VM: C35.1, C40.+, R11.2, U$2.5 (VIN); also elsewhere on the board

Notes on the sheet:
AMS 1117 5V-3.3V Lin. Reg


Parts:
C41: 100uF/35V; 153CLV-0605
D3: B260A-13-F; DO-214AC
R5, R14, R16, R22, R33, R65, R67: 10R; RESISTOR_0603
R6, R17, R18, R30, R34, R66, R72: 10K; RESISTOR_0603
U$1, U$7, U$26, U$28, U$29, U$31, U$33: CONNECTORS_MOLEX-1X2
U$13, U$20, U$27, U$30, U$32, U$34: MOSFET_DMN3404L-7
U$22: MOSFET_AON7524

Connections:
5V: U$29.1, U$31.1, U$33.1; also elsewhere on the board
AVAILABLE7: R65.1; also elsewhere on the board
CONVEYER_SOLENOID: R22.1; also elsewhere on the board
GND: C41.-, R6.1, R17.1, R18.1, R30.1, R34.1, R66.1, R72.1, U$13.P$2 (S1), U$20.P$2 (S1), U$22.1 (S1), U$22.2 (S1), U$22.3 (S1), U$27.P$2 (S1), U$30.P$2 (S1), U$32.P$2 (S1), U$34.P$2 (S1); also elsewhere on the board
LEDSIGNAL1: R16.1; also elsewhere on the board
LEDSIGNAL2: R33.1; also elsewhere on the board
LEDSIGNAL3: R14.1; also elsewhere on the board
unnamed: R16.2, R17.2, U$13.P$3 (G1)
unnamed: R33.2, R34.2, U$20.P$3 (G1)
unnamed: R5.2, R6.2, U$22.4 (G1)
unnamed: R14.2, R18.2, U$27.P$3 (G1)
unnamed: R22.2, R30.2, U$30.P$3 (G1)
unnamed: R65.2, R66.2, U$32.P$3 (G1)
unnamed: R67.2, R72.2, U$34.P$3 (G1)
PUMPS-SIGNAL: R5.1; also elsewhere on the board
TOP-LED-POWER: U$20.P$1 (D1), U$26.2
TOP-LED-POWER1: U$27.P$1 (D1), U$28.2
VIBRATOR_FET_CONTROL1: U$7.2, U$13.P$1 (D1)
VIBRATOR_FET_CONTROL2: D3.2 (A), U$1.2, U$22.5 (D1), U$22.6 (D1), U$22.7 (D1), U$22.8 (D1), U$22.9 (D1), U$22.10 (D1), U$22.11 (D1)
VIBRATOR_FET_CONTROL3: U$29.2, U$30.P$1 (D1)
VIBRATOR_FET_CONTROL4: U$31.2, U$32.P$1 (D1)
VIBRATOR_FET_CONTROL5: U$33.2, U$34.P$1 (D1)
VM: C41.+, D3.1 (C), U$1.1, U$7.1, U$26.1, U$28.1; also elsewhere on the board
Y_END_MIN: R67.1; also elsewhere on the board

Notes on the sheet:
Bottom Leds
Top Leds
VIN PUMP (HIGH CURRENT)
Solenoid 1
Solenoid 2
Solenoid 3

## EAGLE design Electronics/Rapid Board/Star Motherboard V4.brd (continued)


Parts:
C8: 0.1uF; CAP_0603
C67: 10uF; CAP_0603
J3: CONN_04; 1X04
R1, R2, R3, R52, R53: 10K; RESISTOR_0603
S1, S2: SWITCH_MOMENTARY
U$3: CONNECTORS_MOLEX-1X2
U$12: MICROSD_PUSH-PULL

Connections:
3.3V: C8.2, C67.2, J3.2, R1.2, R2.2, R3.2, R52.2, R53.2, U$12.PIN4 (VDD); also elsewhere on the board
GND: C8.1, C67.1, J3.1, S1.3, S1.4, S2.3, S2.4, U$3.2, U$12.G1 (G1-GND), U$12.G2 (G2-GND), U$12.G4 (G4-DET), U$12.PIN6 (VSS); also elsewhere on the board
ISP_BOOT: R53.1, S2.1, S2.2; also elsewhere on the board
RESET: R52.1, S1.1, S1.2, U$3.1; also elsewhere on the board
RX_0: J3.3; also elsewhere on the board
SD_CS: R1.1, U$12.PIN2 (CD/DAT3); also elsewhere on the board
SD_MISO: R2.1, U$12.PIN7 (DAT0); also elsewhere on the board
SD_MOSI: R3.1, U$12.PIN3 (CMD); also elsewhere on the board
SD_SCK: U$12.PIN5 (CLK); also elsewhere on the board
TX_0: J3.4; also elsewhere on the board

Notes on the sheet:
SD Card connector
SD Socket/Comm.
Serial/FTDI
Switches/RST


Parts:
C14, C45, C46, C81: 10uF; CAP_0603
C85, C86: CAP_ARRAY_CA064C104M4RAC7800; CA064_KEM
D2, D5, D6, D7, D8, D9, D10, D11: 1N4148WSTR; SOD-323
J12: FEMALE 2x3; 2X3
J13: 2X6 FEMALE; 2X6
L1, L2, L3: GREEN; LED-0603
LED10: GREEN; LED-0603
R12, R13, R49, R64, R73: 1k; RESISTOR_0603
R20, R24, R31, R32: 4K7; RESISTOR_0603
RN1: YC248-JR-0710KL; YC248JR0710KL
SD: GREEN; LED-0603

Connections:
3.3V: RN1.1, RN1.3, RN1.5, RN1.7, RN1.9, RN1.11, RN1.13, RN1.15; also elsewhere on the board
5V: J12.3, J12.4; also elsewhere on the board
AGND: C14.2, C45.2, C46.2, C81.2; also elsewhere on the board
AVCC: R20.2, R24.2, R31.2, R32.2; also elsewhere on the board
ENDSTOP1: C86.4, D7.A, RN1.16; also elsewhere on the board
ENDSTOP2: C86.3, D2.A, RN1.14; also elsewhere on the board
ENDSTOP3: C86.2, D5.A, RN1.12; also elsewhere on the board
ENDSTOP4: C86.1, D6.A, RN1.10; also elsewhere on the board
ENDSTOP5: C85.4, D8.A, RN1.8; also elsewhere on the board
ENDSTOP6: C85.3, D9.A, RN1.6; also elsewhere on the board
ENDSTOP7: C85.2, D10.A, RN1.4; also elsewhere on the board
ENDSTOP8: C85.1, D11.A, RN1.2; also elsewhere on the board
GND: C85.5, C85.6, C85.7, C85.8, C86.5, C86.6, C86.7, C86.8, J12.1, J12.2, J13.1, J13.3, J13.5, J13.7, J13.9, J13.11, L1.C, L2.C, L3.C, LED10.C, SD.C; also elsewhere on the board
LED1: R12.2; also elsewhere on the board
LED2: R13.2; also elsewhere on the board
LED3: R49.2; also elsewhere on the board
LED4: R64.2; also elsewhere on the board
unnamed: D7.C, J13.2
unnamed: D2.C, J13.4
unnamed: D5.C, J13.6
unnamed: D6.C, J13.8
unnamed: D8.C, J13.10
unnamed: LED10.A, R73.1
unnamed: D10.C, J12.6
unnamed: D11.C, J12.5
unnamed: D9.C, J13.12
unnamed: R64.1, SD.A
unnamed: L3.A, R49.1
unnamed: L2.A, R13.1
unnamed: L1.A, R12.1
PLAY_LED: R73.2; also elsewhere on the board
VAC1: C46.1, R31.1; also elsewhere on the board
VAC2: C14.1, R20.1; also elsewhere on the board
VAC3: C45.1, R24.1; also elsewhere on the board
VAC4: C81.1, R32.1; also elsewhere on the board

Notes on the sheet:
Endstops
LED's
Vacuum Sensors


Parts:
C26, C29: 10uF; C0805
C30, C31, C32, C52: 0.1uF; CAP_0603
C51, C72: 18pF; CAP_0603
C53: 1nF; CAP_0603
D1: B260A-13-F; DO-214AC
J1: C2341
J2: 73725-0110BLF; 737250110BLF
J15: CONN_03; 1X03
R19, R68: 1Mohm; RESISTOR_0603
R69: 12K/1%; RESISTOR_0603
R70, R71: 56K/1%; RESISTOR_0603
U$11: USB-B-PTH
U$14, U$15, U$18, U$19, U$50, U$51, U$56, U$57, U$58, U$59: DIODE_ESD_ESD9B3.3ST5G
U$44: USB_HUB_2.0_4-PORT_USB2514B-I/M2
U$60: CRYSTAL_XRCGB24M000F0L00R0

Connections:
3.3V: C30.1, C31.1, C32.1, U$44.5 (VDDA33), U$44.10 (VDDA33), U$44.15 (VDD33), U$44.23 (VDD33), U$44.26 (RESET_N), U$44.27 (VBUS_DET), U$44.29 (VDDA33), U$44.36 (VDDA33); also elsewhere on the board
5V: C26.2, C29.2, C52.1, D1.1 (C), J1.1, J1.8, J2.1; also elsewhere on the board
5VUSB: D1.2 (A), J15.2
D5_N: U$11.D-, U$44.30 (USBDM_UP), U$58.2
D5_P: U$11.D+, U$44.31 (USBDP_UP), U$59.2
GND: C26.1, C29.1, C30.2, C31.2, C32.2, C51.2, C52.2, C53.1, C72.2, J1.4, J1.5, J2.4, R19.1, R69.1, R70.1, R71.1, U$11.GND, U$14.1, U$15.1, U$18.1, U$19.1, U$44.22 (SDA/SMBDATA/NON_REM1), U$44.24 (SCL/CFG_SEL0/SMBCLK), U$44.37 (VSS), U$50.1, U$51.1, U$56.1, U$57.1, U$58.1, U$59.1; also elsewhere on the board
unnamed: C53.2, J1.MH1, J1.MH2, J1.MH3, J1.MH4, J2.MH1, J2.MH2, J2.MH3, J2.MH4, R19.2
unnamed: C51.1, R68.2, U$44.33 (XTALIN/CLKIN), U$60.1 (2)
unnamed: C72.1, R68.1, U$44.32 (XTALOUT), U$60.3 (1)
unnamed: R69.2, U$44.35 (RBIAS)
unnamed: R70.2, U$44.28 (SUSP_IND/LOCAL_PWR/NON_REM0)
unnamed: R71.2, U$44.25 (HS_IND/CFG_SEL1)
SMOOTHIE_USB_N: U$44.1 (USBDM_DN1/PRT_DIS_M1), U$56.2; also elsewhere on the board
SMOOTHIE_USB_P: U$44.2 (USBDP_DN1/PRT_DIS_P1), U$57.2; also elsewhere on the board
USB1_N: J1.7, U$18.2, U$44.3 (USBDM_DN2/PRT_DIS_M2)
USB1_P: J1.6, U$19.2, U$44.4 (USBDP_DN2/PRT_DIS_P2)
USB2_N: J1.2, J2.2, U$14.2, U$44.6 (USBDM_DN3/PRT_DIS_M3), U$44.8 (USBDM_DN4/PRT_DIS_M4), U$50.2
USB2_P: J1.3, J2.3, U$15.2, U$44.7 (USBDP_DN3/PRT_DIS_P3), U$44.9 (USBDP_DN4/PRT_DIS_P4), U$51.2
VUSB: J15.1, U$11.VBUS

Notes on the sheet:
DOWN Upward Camera
DOWN Downward Camera
DOWN Automatic Feeders
DOWN Smoothieboard


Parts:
C54: 0.1uF; CAP_0603
C55, C56, C57: 10uF; C0805
J4: CONN_04; 1X04
J9, J10: CONN_03X22X3_SILK_MALE_PTH; 2X3
J17: CONN_02; 1X02
R27: 10K; RESISTOR_0603
U3: DRV8833PWPR; DRV8833

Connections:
5V: C54.1, C56.1, C57.1, J9.2, J10.2, R27.2, U3.P$12 (VM); also elsewhere on the board
!SLEEP: R27.1, U3.P$1 (NSLEEP)
CONVEYER-BOARD-STOP: J4.2; also elsewhere on the board
CONVEYER-DOWN-IN: J4.3; also elsewhere on the board
CONVEYER-IN-SENSE: J10.6; also elsewhere on the board
CONVEYER-MOTOR-1A: U3.P$10 (B_IN2); also elsewhere on the board
CONVEYER-MOTOR-1B: U3.P$9 (B_IN1); also elsewhere on the board
CONVEYER-OUT1: J9.3, J10.5, U3.P$5 (B_OUT2)
CONVEYER-OUT2: J9.5, J10.3, U3.P$7 (B_OUT1)
CONVEYER-OUT-SENSE: J9.6; also elsewhere on the board
CONVEYER-UP-OUT: J4.4; also elsewhere on the board
GND: C55.2, C56.2, C57.2, J4.1, J9.4, J10.4, U3.P$3 (A_ISENSE), U3.P$6 (B_ISENSE), U3.P$13 (GND), U3.P$17 (GND(THRML)); also elsewhere on the board
GRIPPER-ENCODER2: J9.1, J10.1; also elsewhere on the board
unnamed: C54.2, U3.P$11 (VCP)
unnamed: C55.1, U3.P$14 (VINT)
unnamed: J17.2, U3.P$4 (A_OUT2)
unnamed: J17.1, U3.P$2 (A_OUT1)
NOZZLE-MAGAZINE1: U3.P$15 (A_IN2); also elsewhere on the board
NOZZLE-MAGAZINE2: U3.P$16 (A_IN1)

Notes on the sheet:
Conveyer Pins


Board: 4 copper layers, 100.0 x 75.0 mm, 271 parts (0 on the bottom side), 225 nets.

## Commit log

2021-09-19 Create Rapid Board Connections.png
2021-09-20 Electronics update
    Added feeder motherboard and extensions
    [Rapid_Feeder_Master_RS485_small_v2.brd, Rapid_Feeder_Master_RS485_small_v2.sch, Rapid_Feeder_Master_RS485_traces_Star.brd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]
2021-09-20 Updated files
    [Rapid_Feeder_Master_RS485_small_v2.brd, Rapid_Feeder_Master_RS485_small_v2.sch]
2021-09-21 Added IC Tray
    [PNP - Tray Base.brd, PNP - Tray Base.sch, PNP - Tray_ICs.brd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]
2021-09-30 Updated settings
    Added support for nozzle angle offsets and updating MOVE_TO_COMMAND to include angles.
2021-10-01 Added lens calibration pcb
    PCB used to calibrate upward looking camera by running it through a gcode file that will maneuver it around the upward looking camera for lens distortion calibration.
    [Lens Calibration.brd, Lens Calibration.sch]
2021-10-01 Upward Cam Gcode Path
    Added path for nozzle to take when doing lens calibration for upward camera.
2021-10-02 Updated to include 5mm cube
    [Lens Calibration.brd]

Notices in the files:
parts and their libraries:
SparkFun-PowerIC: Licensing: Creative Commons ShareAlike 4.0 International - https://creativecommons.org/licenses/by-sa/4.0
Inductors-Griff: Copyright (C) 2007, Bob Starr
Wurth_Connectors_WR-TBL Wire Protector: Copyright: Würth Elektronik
